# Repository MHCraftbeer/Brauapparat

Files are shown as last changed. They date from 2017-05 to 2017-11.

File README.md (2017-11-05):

# Brauapparat mit interner Steuerung (Entwicklung eingestellt)
(zum neuen Projekt "BierBox (Brauapparat mit externer Steuerung)" gehts hier entlang https://github.com/MHCraftbeer/BierBox)

mehr Infos auf meinem Blog: 
https://mhcraftbeer.wordpress.com/

Alle Dateien, Daten, Infos die ich genutzt habe um meinen Brauapparat zu bauen

Gesamtkosten etwa 400€

Zur Einkaufsliste:

Die ist sehr einfach und rudimentär zusammengeschrieben und soll nur ungefähr vermitteln was gebraucht wird und wieviel das kostet.
Ich persönlich verwende vieles vom Schrottplatz. Dort kann man, besonders was Teile aus Edelstahl angeht, sehr sehr viel sparen.
Zum läutern verwende ich zum Beispiel nicht den Leuterator aus der Einkaufsliste, sondern das Edelstahlgeflecht eines Panzerschlauches. Den Rührer habe ich mir selber in einer Studierendenwerkstatt mit einem WIG Schweißgerät zusammengeschweißt.

Zusätzlich braucht man auch noch Werkzeug: Akkuschrauber, versch. Bohrer, Lötkolben, (Schweißgerät, Gewindeschneideisen, Schraubstock, usw.)
Kleinkram wie verschiedene Schrauben und Muttern (besonders zum Befestigen des Wischermotors) habe ich zusammengefasst.

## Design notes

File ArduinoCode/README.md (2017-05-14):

Code für den Arduino

Belegt etwa 85% des Speichers eines Arduino Uno. Mehr Code führt zu Problemen beim Ein- und Ausschalten der Relais.

Verwendet wurde ein "4 Relay Module" und ein "LCD Keypad Shield".
Bis auf Pin A6 und A7 sind alle Pins belegt.

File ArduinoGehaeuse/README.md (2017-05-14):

# Alles für das Arduino Gehäuse
Das Gehäuse wurde mit einem Lasercutter eines nahegelegenen Fablabs aus einer 3mm MDF Platte geschnitten (ca. so groß wie ein Din A4 Blatt).
Die Datei für den Lasercutter kann man mit Inkscape öffnen.
Es wurde mit 4 Schrauben M4x50 am Einkochtopf befestigt.
Zwischen Gehäuse und Keinkochtopf wurde 3mm dickes Moosgummi als Dichtung verwendet.

Die Buttons wurden ebenfalls im fablab 3D gedruckt.
Es werden 3 normale Buttons und 1 Reset Button benötigt.
Die Datei kann jeder Windows 10 PC öffnen.

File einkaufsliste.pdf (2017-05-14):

Posten | Preis
Weck WAT25 Einkochautomat | | 100
Messbecher 5L | | 5
Holzlöffel, 70 cm | | 6
Arduino Uno (nicht original) | | 10
LCD keypad Shield | | 10
4 Kanal Relais Modul | | 7
Netzteil Rührer 12V, 6A | | 15
Golf 4 Wischermotor (gebraucht) | | 15
Leuterator Comfort für Einkocher | | 45
Silikonschlauch 1/2" 2m | | 5
Rührer | ??
Wärmeleitpaste | | 2
NTC Thermistor 10kOhm | 2x | 4
Widerstand 10kOhm | 2x | 0,5
Wasserdichte Steckverbindung, 3 Pol | | 6
5mm Leds | 5x | 1
Widerstand 220Ohm | 5x | 1
Netzteil Arduino 5V, 1A | | 10
Adapter M24x1 auf 3/4" | | 6
Schlauchtülle 3/4" auf 10mm | | 3
Kühlspirale (od. Wärmetauscher) | | 70
PVC Schläuche und Fittings | | 20
Manometer 1/8" | | 10
Adapter M5 auf 1/8" | | 1
versch. Schrauben und Muttern | | 20

372,5

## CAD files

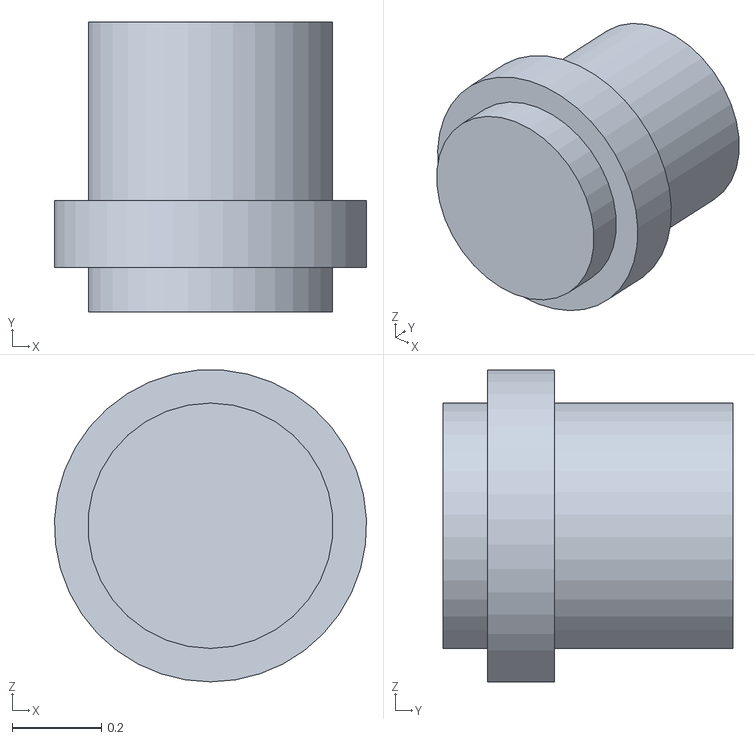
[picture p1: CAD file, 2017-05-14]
ArduinoGehaeuse/Button.stl
0.699 x 0.65 x 0.699

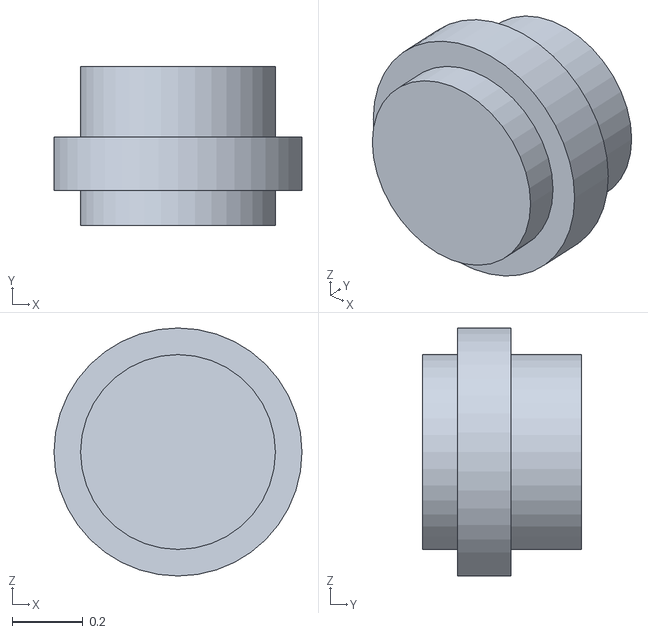
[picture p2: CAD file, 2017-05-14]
ArduinoGehaeuse/Reset Button.stl
0.7 x 0.45 x 0.7

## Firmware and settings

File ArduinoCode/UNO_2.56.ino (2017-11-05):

////////////////
////////////////
////////////////
//Reizt den Uno ziemlich aus, Programmspeicher und Variablen sind zu 85% belegt
//Wenn der Programmspeicherplatz mit mehr als 85% belegt wird funktionieren die Relais nicht mehr, wohl wegen den unsigend longs die überlaufen
//mit lCD Keypad shield sind alle nutzbaren Pins außer A6 und A7 vom Uno belegt. mehr geht nicht.
//beim shield wurde der poti für den kontrast nach hinten verlegt und die icsp pins abgebrochen
//der button right wird nicht verwendet
/*Changelog
 * 2.01 Temperaturmessungen, Heizungsregelung, Buzzer, Timer, Button, Automatik Start, Automatik
 * 2.02 Automatik verbessert, allg. Verbesserungen
 * 2.03 Rührersteuerung integriert, Hopfentimer, Hopfengaben Reminder, Manuell, allg. Verbesserungen
 * 2.04 Signal LEDs für Blende, allg. Verbesserungen
 * 2.05 allg. Verbesserugen, mit GoBetwino angefangen
 * 2.06 GoBetwino integriert (Arduino sendet über USB LogDaten an gobetwino.exe und speichert sie in Datei; http://www.mikmo.dk/gobetwino.html), globale Variablen nachvollziehbarer gemacht, Changelog erstellt, allg. Verbesserungen
 *2.07 paar Bugs entfernt: LED Takt OK, Buzzer Takt OK;
 *2.08 LCD Keypad Shield Steuerung wieder eingebaut, Variablen im Sketch nach oben gestelllt, Keypad funktioniert, Manueller Modus bis auf Timer auch schon
 *2.09 manueller modus fertig, manuellen alarm und meldung eingebaut
 *2.10 manueller modus komplestt fertig, mit automaischen angefangen
 *2.11 viel rumprobieren und fehlersuche
 *2.12 manueller modus und automaisch modus sind komplett fertig und funktionieren 1a
 *2.2 alles läuft soweit ich es feststellen kann
 *2.21 versuche schnelleinstellung für hohe zahlen einzubauen
 *2.3 schnelleinstellung für hohe zahlen fertig eingebaut. alles soweit funktionsfähig. fertig???????
 *2.31 bugs bei automaischen und autokochen beseitigt
 *2.32 gobetwino überarbeitet
 *2.34 NTCs genauer machen
 *2.40 Keine bugs mehr gefunden, soweit ist alles bereit für die generalprobe. lediglich die ausgangswerte müsste man noch anpassen.
 *2.41 Referenzwiderstand von tempT auf 7640 Ohm geändert (ja der ist laut multimeter wirklich so gering)
 *2.42 Gradientenberechnung der Heizungsregelung angepasst. Gradient ist jetzt wirklich K/min. Automaischen, Eingemaischt wird jetzt nach erreichen der temperatur und nicht nach ablauf des ersten timers.
 *2.43 ausprobieren einer pid regelung: http://playground.arduino.cc/Code/PIDLibrary, hat nicht funktioniert
 *2.50 alles funktioniert. Programmspeicher darf 85% nicht überschreiten, sonst funktioniert das relais nicht mehr
 *2.51 Maximaltemperatur auf 102°C erhöht, Referenzwiderstand des Temperatursensors auf 100°C kalibriert
 *2.52 Wenn Kochtemp >= 100 °C ist dann ist die Heizung ununterbrochen eingeschalten, hoch und runterpfeile in Statusmenüs entfernt, heizung ist jetzt mindestens für 5 sekunden an, Softwarenummer im statusmenue angezeigt
 *2.53 hoch und runterpfeile wieder im Statusmenü, temperatur auf eine nachkommastelle gerundet, fehler bei der anzeige behoben
 *2.54 Rührer aus wenn beim kochen hundert grad erreicht werden um den deckel zu wechseln, tempSollErreicht beim kochen für 99,5 grad festgelegt, eingabe max und min beim kochen angepasst, K wert auf 0,75 erhöht
 *2.55 Timer sollten die Laufzeit des Programms jetzt berücksichtigen und dadurch genauer sein, unnötige unsigned long Varibalen zu int gemacht, Gobetwino Ausgabe auf gerundete Temperaturwerte angepasst
 *2.56 timer änderungen von 2.55 wieder rückgängig gemacht, da der Timer so nur noch ungenauer wurde, pin belegung geändert, Referenzwiderstand von NTC der Elektronik geändert (= der des Topfes)
 */
 float software = 2.56;
 /*TODO:
 *  -Erledigt: Heizungsregelung einstellen dh. richtigen Kwert finden. 
 *  -Erledigt: Temperaturmessung kalibrieren dh. Referenzwiderstand richtig einstellen. mit 100°C kalibriert
 *  -Erledigt: Abkühlung druch das Malz mit einbeziehen, dh den timer vom zweiten automaischen Schritt gleich nach dem einmaischen zu starten und nicht erst wenn die temp erreicht wurde
 *  -Erledigt: min und max werte an reale werte anpassen 
 *  -Erledigt: gobetwino testen
 *  -Erledigt: standardmäßg rührer stufe 0 ist nervig, eigentlich muss immer gerührt werden
 *  -Erledigt (hat aber nicht funktioniert, messung war mit gemessenem Widerstand total falsch):genauen Referenzwiderstand messen
 *BUGS:
 *- Behoben: timer für die zweite rast wartet nicht auf die einmaischenfertig bestätigung sondern fängt gleich an
 *- Behoben: nach einem durchlauf manuell lässt sich kein zweiter starten
 *- Timer ist ungenau, geht etwa eine Minute pro Stunde nach, wahrscheinlich wegen der Laufzeit des Programms
*/
////////////////////////////////////////////////////////////////////////////////////////////////////////////////////////////////////
//////////////////////////////////////////////////// Hardware Ports
//shield
//PORTS OBEN (=die löcher für pins, von links nach rechts)
//D13, D12, D11, D3, D2, --, --, (die letzten beiden nicht benutzen, dann spinnt der arduino)
//PORTS UNTEN (=die löcher für pins, von links nach rechts)
//RST, 3.5V, 5V, GND, GND, Vin
//alles irgendwo anschließen (nur die tempPins brauchen analoge pins)
//dann die belegung über das arduino bsp "blinkwithoutdelay" bestimmen
//und hier entsprechend ändern
//
const byte keypadPin    = A0;  // Analog Keypad an A0
//tempmessung
const byte tempTPin = A1;
const byte tempIPin = A2;
//relais (einfach über bsp "blinkwithoutdelay" bestimmen)
const byte ruehrerPin1 = A5;
const byte ruehrerPin2 = A3;
const byte heizungPin = A4;
//buzzer
const byte buzzerPin = 2;
//leds (einfach über bsp "blinkwithoutdelay" bestimmen)
const byte ruehrerLed1 = 3;
const byte ruehrerLed2 = 11;
const byte heizungLed = 13;
const byte programmLed = 12;
//////////////////////////////
///////////////////////////////
///////////////////////////////
////////////////////////////////////////////////////////////////////////////////////////////////////////////////////////////////////
//////////////////////////////////////////////////// Variablen
//
//////////////////////////////////////////////////////////////////////////////Eingabe
byte tempMin = 35; //minimal Temperatur
byte tempMax = 85;
byte tempKochenMin = 90;
byte tempKochenMax = 102;
byte timerMin = 5; //minimal Timer
byte timerMax = 180;
byte timerKochenMin = 45;
int zaehlerTakt = 150; //alle x ms steigt der zähler um eins
unsigned long zaehlerStart = 0;
byte button;
boolean buttonPressed = false;
boolean meldung = false;
boolean automatikBestaetigung = false;
//
//////////////////////////////////////////////////////////////////////////////TemperaturSensoren
long samplesT[20];
long samplesI[5];
unsigned long sensorPreviousTime = 0;
//////////////////////////////////////////////////////////////////////////////Heizungsregelung
float k = 0.75; //Gradientenfaktor
int heizungESV = 10000; //Pause zwischen Aus- und Einschalten der Heizung
int heizungMesszyklus = 5000; //Abstand der Temperaturmessung für die Gradientenberechnung
boolean heizungOFF = false;
byte tempSoll = tempMin;
byte tempSensorDaempfung = 0; //dämpft überschwingen vom Temperatursensor
unsigned long heizungVorherigeZeit = 0; //Zeit bei t-1
float heizungVorherigeTemp = 0; //Temp bei t-1
unsigned long heizungWarten = 0; //Wartezeitmessung Start
boolean tempSollErreicht = false;
//
/////////////////////////////////////////////////////////////////////Rührersteuerung
int ruehrerPause = 1000; //stufe 2 benötigt stufe 1 um zu starten, stufe 1 läuft ruehrerpause lang bis stufe 2 startet
boolean ruehrerStart = false;
boolean ruehrerOFF = false;
byte ruehrerStufe = 1;
boolean ruehrerStufe1Gewartet = false;
boolean ruehrerPauseGestartet = false;
unsigned long ruehrerPreviousMillis;
//
////////////////////////////////////////////////////////////////////////////Buzzer Takt
int buzzerFrequenz = 831; //buzzerFrequenz des Peips in Hz
byte buzzerDauer = 150; //Piep-Dauer in ms
byte buzzerIntervall = 200; //Pause zwischen Piep in ms
boolean alarmOFF = false;
boolean alarmON = false;
unsigned long buzzerPreviousMillis = 0;
boolean buzzerON = false;
//
/////////////////////////////////////////////////////////////////////Led Takt
int ledIntervall = 1000; //zeit welche die led aus und an ist
unsigned long ledPreviousMillis = 0;
boolean ledON = false;
//
//////////////////////////////////////////////////////////////////////////////////////Timer
boolean datenUebergeben = false;
int timerMinuten;  //minutenanzeige
boolean timerStart = false;
int timerManuell = timerMin;
byte timerSekunden = 0; //sekundenanzeige
unsigned long timerSet = timerMin;
unsigned long timerPreviousMillis = 0;
boolean timerEnde = false;
//
///////////////////////////////////////////////////////////////////////////////////Hopfen Timer
unsigned long timerHopfenSet = timerMin;
unsigned long timerHopfenPreviousMillis = 0;
boolean timerHopfenEnde = false;
int timerHopfenMinuten;
boolean timerHopfenStart = false;
byte timerHopfenSekunden;
//
//////////////////////////////////////////////////////////////////////////////////AutoMaischen Modus
boolean einmaischenPause = false;
boolean keinHopfenMehr = false;
byte autoMaischenStatus = 1; //für Statusanzeige auf display
boolean autoMaischenStartDruecken = false;
boolean autoMaischenStart = false;
boolean autoMaischenEnde = false;
boolean jetztLaeutern = false;
byte tempEinmaischen = tempMin;
byte tempStep1 = tempMin;   //StartTemperaturen
byte tempStep2 = tempMin; 
byte tempStep3 = tempMin; 
byte tempStep4 = tempMin; 
byte tempStep5 = tempMin; 
byte tempStep6 = tempMin; 
int timerStep1 = timerMin;  //StartTimer Min
int timerStep2 = timerMin;
int timerStep3 = timerMin;
int timerStep4 = timerMin;
int timerStep5 = timerMin;
int timerStep6 = timerMin;
boolean einmaischenJetzt = false;
boolean einmaischenFertig = false;
byte currentStep = 1;
byte letzterStep;
byte tempStepMax; //maximaltemperatur während automatik
int timerStepMax;  //gesamtdauer der automatik
boolean maximaMaischen = false;  //berechnet die drei vorherigen werte
//
//////////////////////////////////////////////////////////////////////////////////AutoKochen Modus
int timerKochen = timerKochenMin;
byte tempKochen = tempKochenMin;
byte autoKochenStatus = 1; //für Statusanzeige auf display
boolean autoKochenStartDruecken = false;
int timerHopfen1 = timerMin;
int hopfenAlarm1;
int hopfenAlarm2;
int hopfenAlarm3;
int hopfenAlarm4;
int timerHopfen2 = timerMin;
int timerHopfen3 = timerMin;
int timerHopfen4 = timerMin;
int timerHopfen5 = timerMin;
boolean maximaKochen = false;
boolean autoKochenStart = false;
boolean autoKochenEnde = false;
byte hopfen = 1;
byte letzterHopfen = 1;

byte autoKochenMenue = 1;
//
//////////////////////////////////////////////////////////////////////////////Manueller Modus
boolean manuellStart = false;
byte manuellTemp = tempMin;
boolean manuellEnde = false;
//
/////////////////////////////////////////////////////////////////////////////Status Menü
byte statusMenue = 1;
//
///////////////////////////////////////////////////////////////////////////////GoBetwino
boolean logGestartet = false;
int runtime;
int gobetwinoIntervall = 10000; //Übertragungsintervall
int logTime = 0;
unsigned long logPreviousMillis = 0;
//
////////////////////////////////////////////////////////////////////////////Userinterface
byte hMenueMax = 4;
byte manuellMenue = 1;
byte autoMaischenMenue = 1;
boolean hMenueON = true;
boolean nMenueON = false;
byte hMenue = 1;
byte nMenue = 1;
byte meldungsNummer = 1;
byte ae[8] ={ //Buchstabe "ä"
  B01010,
  B00000,
  B01110,
  B00001,
  B01111,
  B10001,
  B01111,};
byte ue[8] ={ //Buchstabe "ü"
  B01010,
  B00000,
  B10001,
  B10001,
  B10001,
  B10011,
  B01101,};
byte grad[8] ={ //Grad Zeichen
  B00010,
  B00101,
  B00010,
  B00000,
  B00000,
  B00000,
  B00000,};
byte pfeil[8] = { //Größer Zeichen, OK
  B00000,
  B00100,
  B00010,
  B00001,
  B00010,
  B00100,
  B00000,};
byte up[8] = { //Pfeil Zeichen hoch
  B00000,
  B00000,
  B00100,
  B01010,
  B10001,
  B00000,
  B00000,};
byte down[8] = { //Pfeil Zeichen runter
  B00000,
  B00000,
  B00000,
  B10001,
  B01010,
  B00100,
  B00000,};
byte soll[8] = { //Pfeil rechts
  B00000,
  B00100,
  B00010,
  B11111,
  B00010,
  B00100,
  B00000,};
  
////////////////////////////////////////////////////////////////////////////////////////////////////////////////////////////////////
////////////////////////////////////////////////////Bibliotheken einbinden
#include <LiquidCrystal.h>
LiquidCrystal lcd(8, 9, 4, 5, 6, 7);
#define NONE       0  //kein Button wird gedrückt
#define RIGHT      1 //RIGHT (ungenutzt)
#define HOCH       2 //UP
#define RUNTER     3 //DOWN
#define OK         4 //LEFT
#define ZURUECK    5 //SELECT
/////////////////////////////////////////////////////////////////////////////////////////////////////////////////////////////////////
/////////////////////////////////////////////////////////////////////////////////////////////////////////////////////////////////////
/////////////////////////////////////////////////////////////////////////////////////////////////////////////////////////////////////
/////////////////////////////////////////////////////////LCD Keypad Shield///////////////////////////////////////////////////////////
/////////////////////////////////////////////////////////////////////////////////////////////////////////////////////////////////////
/////////////////////////////////////////////////////////////////////////////////////////////////////////////////////////////////////
/////////////////////////////////////////////////////////////////////////////////////////////////////////////////////////////////////
//Button eingaben
int x;
int keypad() {
  
    x = analogRead(keypadPin);
    if (x > 1000) return NONE;
    else if (x < 200) return HOCH;
    else if (x < 520) return RUNTER;
    else if (x < 700) return OK;
    else if (x < 1000) return ZURUECK;
    else return NONE;
}
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
void loop() {
  unsigned long start = micros();
  //
  //schaltet programme ein
  //serial();  //Aktiviert serielle Ausgaben für den Monitor
  timer();  //startet Timer für die gesamt Dauer
  eingabe();  //aktiviert die Eingabe durch buttons
  userInterface(); //Aktiviert das Userinterface
  autoMaischen(); //aktiviert Automaischen modus
  autoKochen();  //aktiviert Autokochen modus
  manuell(); //aktiviert den manuellen Modus
  //
  //schaltet die programmLed aus und ein
  if ((manuellStart || autoMaischenStart || autoKochenStart) && ledTakt() == true) digitalWrite(programmLed, HIGH); //schaltet automatik LED aus und ein
    else digitalWrite(programmLed, LOW);
  //
  //
  //Schaltet die Heizung aus und ein
  if (heizung() == true && !heizungOFF){
    digitalWrite(heizungPin, LOW);  //schaltet Heizung ein
    digitalWrite(heizungLed, HIGH); //schaltet heizungLed ein
  }
    else {
      digitalWrite(heizungPin, HIGH);   //schaltet Heizung aus
      digitalWrite(heizungLed, LOW); //schaltet heizungLed aus
    }
  //
  //Schaltet den Rührer aus und ein
  if (ruehrerStufe1() == true) { //schaltet rührer stufe 1 ein
    digitalWrite(ruehrerPin1, LOW);
    digitalWrite(ruehrerLed1, HIGH);
  }
    else {  //schaltet rührer stufe 1 aus
      digitalWrite(ruehrerPin1, HIGH);
      digitalWrite(ruehrerLed1, LOW);
    }
  if (ruehrerStufe2() == true) { //schalte rührer stufe 2 ein
    digitalWrite(ruehrerPin2, LOW);
    digitalWrite(ruehrerLed2, HIGH);
  }
    else {    //schaltet rührer stufe 2 aus
      digitalWrite(ruehrerPin2, HIGH);
      digitalWrite(ruehrerLed2, LOW);
    }
  //
  //Schaltet den Buzzer aus und ein
  if (buzzer() == true  && alarmON) tone(buzzerPin, buzzerFrequenz, buzzerDauer);
  //
  //Schaltet GoBetwino aus und ein
  if (autoMaischenStart || autoKochenStart || manuellStart) gobetwino();
  //
  //LED und Buzzer Test über statusmenü
  if (ledTest() == true) {
    if (buzzer() == true) tone(buzzerPin, buzzerFrequenz, buzzerDauer);
    digitalWrite(ruehrerLed1, HIGH);
    digitalWrite(ruehrerLed2, HIGH);
    digitalWrite(programmLed, HIGH);
    digitalWrite(heizungLed, HIGH);
  }
runtime = micros() - start;
}

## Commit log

2017-05-30 Add files via upload
    *2.52 Wenn Kochtemp >= 100 °C ist dann ist die Heizung ununterbrochen eingeschalten, hoch und runterpfeile in Statusmenüs entfernt, heizung ist jetzt mindestens für 5 sekunden an, Softwarenummer im statusmenue angezeigt
    *2.53 hoch und runterpfeile wieder im Statusmenü, temperatur auf eine nachkommastelle gerundet, fehler bei der anzeige behoben
    *2.54 Rührer aus wenn beim kochen hundert grad erreicht werden um den deckel zu wechseln, tempSollErreicht beim kochen für 99,5 grad festgelegt, eingabe max und min beim kochen angepasst, K wert auf 0,75 erhöht
    [_2.54.ino]
2017-05-30 Add files via upload
    *2.55 Timer sollten die Laufzeit des Programms jetzt berücksichtigen und dadurch genauer sein, unnötige unsigned long Varibalen zu int gemacht, Gobetwino Ausgabe auf gerundete Temperaturwerte angepas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
2017-06-01 Delete _2.55.ino
    Timer hat nach Änderung schlechter funktioniert
